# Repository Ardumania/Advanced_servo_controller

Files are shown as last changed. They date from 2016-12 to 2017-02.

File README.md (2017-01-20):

# Advanced_servo_controller
Based on ATtiny85 and PJON bus

In the last years I have worked in several projects related with education and robotics 
and I have found several problems, if you work with only one microcontroller you are very 
limited about the number of servos you can drive, you need a separate controller to 
drive until 32 servos, but it’s still possible. What about sensors? if you are planning 
to build an hexapod and mount two distance sensor for each leg It’s practically impossible.

There are systems for robotics that consist in smart servos connected by a RS-485 bus 
(Dynamixel or Ubtech), but in these systems is not possible to implement sensors on the 
same bus. And other problem is that those systems use a closed protocol and developers 
can’t implement their own sensors or actuators.

For several time I was thinking in an alternative system for implement sensors and actuators 
in a same communication bus and, of course, do it open allowing developers and enthusiast to 
design their own modules and share them. Initially thought in I2C bus be cause is well 
documented and easy to use but need 4 wires and there are no standard cable to use, this 
is an inconvenient.

In May 2015 I was talking in Valencia with my mentor and friend David Cuartielles about 
this project and he made me a suggestion: the PJON bus developed by an italian guy 
(Giovanni Blu), it’s one wire, addressable, fully bi-directional and open. That was 
instant love and this project could start.
PJON project can be found here: https://github.com/gioblu/PJON

The main goal of this project is to build a net of modules that can talk to each others
and with the main controller by only a one wire. Just think about it: one wire for data, 
one wire for GND and another wire for VCC, you can have a net of actuators and sensors 
just connected by standard servo wires… and can be connected up to 256 devices.

The first prototype is a servo module, actually called Advanced Servo Controller, and 
is in a very early state of development but it will work for sure be cause the concept 
is very simple: a small pcb with an ATtiny85 that communicates with a main controller 
(Arduino, of course) via a PJON bus, this ATtiny receives commands and generates the 
servo control signals. Commands can be like AT commands, e.g. “GT1500,2000”, this is 
Go To position 1500 in 2000 milliseconds, position is the servo control signal duty 
cycle in microseconds and final time is the time in which must reach that position 
from its actual position… simple. Each module has a current sensor a can send readings 
to the main controller as responses to a specific requests… and more capabilities can 
be implemented in the module firmware in the future.

In the future can be implemented more types of modules with sensors, e.g. distance sensors, 
which are very interesting in robotics.

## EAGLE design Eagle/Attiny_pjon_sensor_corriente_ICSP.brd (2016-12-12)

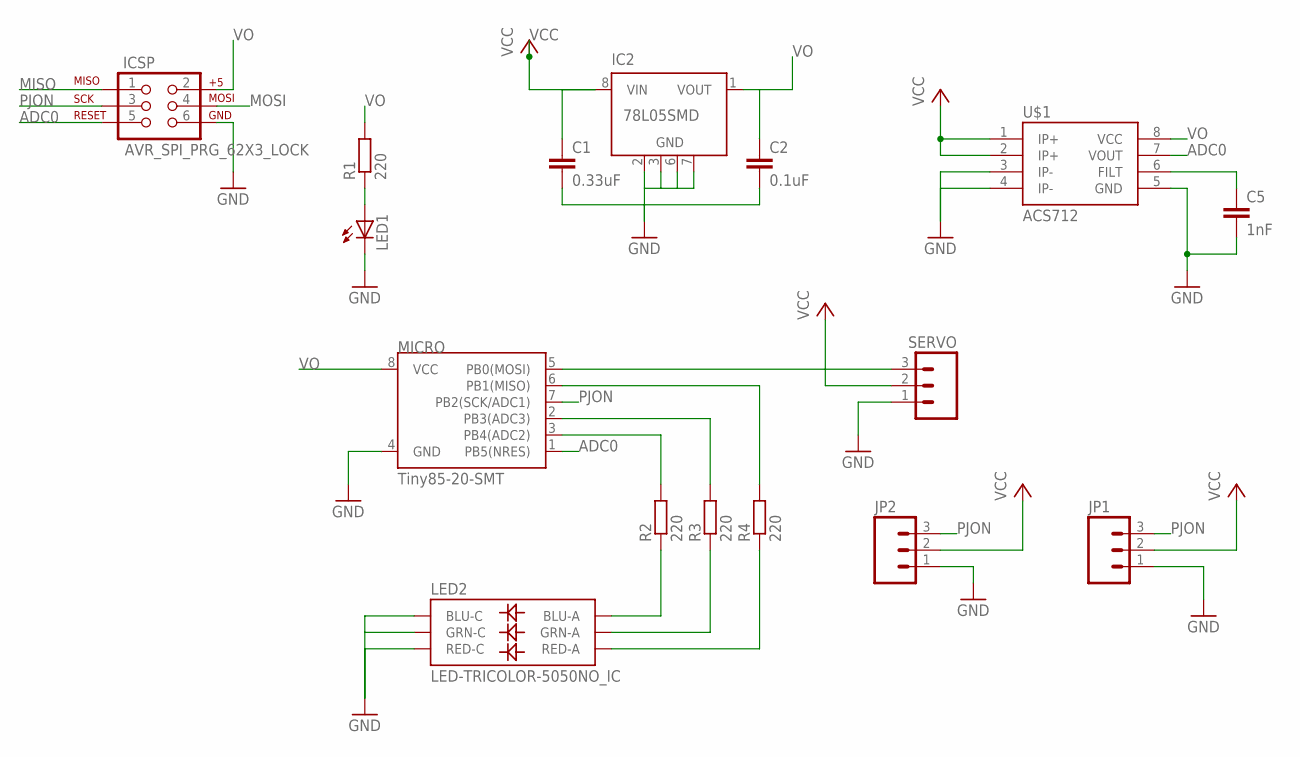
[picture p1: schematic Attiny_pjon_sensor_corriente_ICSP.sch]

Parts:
C1: 0.33uF; C1206
C2: 0.1uF; C1206
C5: 1nF; C1206
IC2: 78L05SMD; SO08
ICSP: AVR_SPI_PRG_62X3_LOCK; 2X3_LOCK
JP1, JP2: M03PTH; 1X03
LED1: LEDSMT1206; 1206
LED2: LED-TRICOLOR-5050NO_IC; LED-TRICOLOR-5050
MICRO: Tiny85-20-SMT; SO08-EIAJ
R1, R2, R3, R4: 220; R1206
SERVO: M03PTH; 1X03
U$1: ACS712; SO08

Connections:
ADC0: ICSP.5, MICRO.1 (PB5(NRES)), U$1.7 (VOUT)
GND: C1.2, C2.2, C5.2, IC2.2 (GND), IC2.3 (GND), IC2.6 (GND), IC2.7 (GND), ICSP.6, JP1.1, JP2.1, LED1.C, LED2.4 (BLU-C), LED2.5 (RED-C), LED2.6 (GRN-C), MICRO.4 (GND), SERVO.1, U$1.3 (IP-), U$1.4 (IP-), U$1.5 (GND)
MISO: ICSP.1, MICRO.6 (PB1(MISO)), R4.2
MOSI: ICSP.4, MICRO.5 (PB0(MOSI)), SERVO.3
unnamed: MICRO.3 (PB4(ADC2)), R2.2
unnamed: C5.1, U$1.6 (FILT)
unnamed: MICRO.2 (PB3(ADC3)), R3.2
unnamed: LED2.3 (BLU-A), R2.1
unnamed: LED2.1 (GRN-A), R3.1
unnamed: LED2.2 (RED-A), R4.1
unnamed: LED1.A, R1.1
PJON: ICSP.3, JP1.3, JP2.3, MICRO.7 (PB2(SCK/ADC1))
VCC: C1.1, IC2.8 (VIN), JP1.2, JP2.2, SERVO.2, U$1.1 (IP+), U$1.2 (IP+)
VO: C2.1, IC2.1 (VOUT), ICSP.2, MICRO.8 (VCC), R1.2, U$1.8 (VCC)

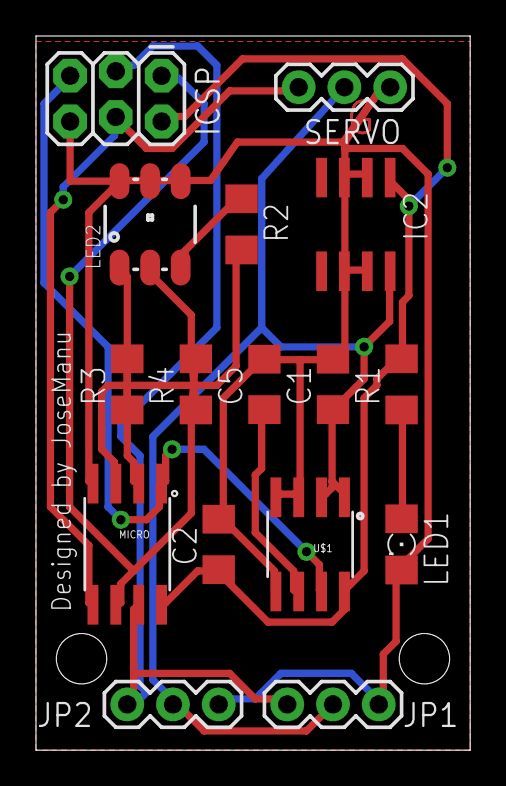
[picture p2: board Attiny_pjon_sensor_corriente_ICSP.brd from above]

Board: 2 copper layers, 24.1 x 39.7 mm, 16 parts (0 on the bottom side), 14 nets.

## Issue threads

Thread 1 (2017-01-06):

External oscillator

gioblu, 2017-01-06:
Ciao, I think could be safer to use an external oscillator to have also large batches of those devices working in the same fashion. Sadly the internal oscillator (or PPL clock) is not so reliable and it can have strong differences  in behaviour, chip to chip. so having some of them not working or operating at a lower performance. Using a 16MHz external oscillator would enable the ATtiny to run SoftwareBitBang at FAST_MODE so at  25157Bd or 3.15kB/s. See https://github.com/gioblu/PJON/wiki/ATtiny-interfacing and https://github.com/gioblu/PJON/issues/25

Ardumania, 2017-01-10:
Hi @gioblu, I am very honored that you follow this project and all your suggestions will be taken into account.
This is the first version of the board and there are many things to change, first of all the RGB LED goes out. Another contributor suggest that will be a great idea to have a temperature sensor on board and I must to put a NTC resistor.
I'm redesigning the board at this moment and it's a good moment for your suggestion, I'm going to put a 16MHz external oscillator.
 I have all the materials for the first version and will mount only 2 or 3 units for test.
Thank you very much.

gioblu, 2017-01-10:
Ciao @Ardumania, I am honored too to see PJON being your choice for this project.
Feel free to contact me for info/support.

gioblu, 2017-01-11:
I forgot to mention, that years ago I worked on a really small Arduino compatible board, based on ATtiny85 (ATtiny85 + 78l05 + 2 caps + LED + resistor) was able to run smoothly cheap servos: https://www.youtube.com/watch?v=PxwNOG1WzhY
In any case, PJON needs the external oscillator, but I think this is an indication that you will be able to achieve your goal, to reduce buzz or jitter:
- Detach servos when not moving
- Power servo not from 5v, but with external power supply 5/6v
- If using common power supply, power servos through a diode, blocking current to flow from the servo to the power supply.

gioblu, 2017-01-11:
@Ardumania, temperature sensor is cool, but would be nice in some cases to have the chance to drive 2 servos, for example where you need to drive 2 wheels precisely (rover robot), so with a single packet it would be possible to start both wheels at a determined speed, at the same time.

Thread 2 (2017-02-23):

Circuit considerations

gioblu, 2017-02-23:
Ciao @Ardumania I have taken a look to the new board schematic you pushed.
I maybe have a wrong feeling but, wouldnt the diode be better positioned before VIN instead of after VOUT? I generally have needed a diode in that configuration to share power supply with a running servo with an arduino. Maybe higher capacitance capacitor on power supply would for sure help to mantain voltage stability.

Ardumania, 2017-02-23:
Ciao @gioblu , I appreciate your suggestions.
With the first circuit version was a problem, when connected the ArduinoISP to program the ATtiny the voltage regulator burned because power of ArduinoISP and voltage regulator output were not compatible. Adding a schottky diode this problem is now solved.
You are right, in this configuration VOUT is 4,5v, the minimum voltage to work, but it works.
My knowledge of electronics are very poor, so I don't know very well what I'm doing, but at this moment woks.
The servo must receive VCC without passing through voltage regulator, i.e. direct power from the battery. I don't understand very well your suggestion about a blocking diode on attiny side but I will search about information about this, as I said I'm a little lost with electronics.
In few days I will start to work with a small servo.
Thank you.

gioblu, 2017-02-23:
@Ardumania  I am sorry for the italianizations hehe :).

I would try to feed the voltage regulator though a diode positioned there to "block" inverse current before the power supply stage, removing the diode you now have on VOUT. And with this you should have shielded your regulator VOUT by strong voltage oscillations due to the servo running. I do think that in this configuration the servo motor voltage drop would affect less the capacitors, so giving you a more stable VOUT. I agree that the servo shouldnt be powered by the voltage regulator, because it has its own.

I have never had a 7805 / 78l05 burning for that reason, are you sure there was some other hidden issue? In general if flashed from another arduino and arduinoISP 78l05 survives and should work fine without any additional hardware in that configuration.

Consider that a lower than 5 volts affects the maximum distance range you can get with PJON communication range to have 5v as a reference to avoid to affect PJON communication range.

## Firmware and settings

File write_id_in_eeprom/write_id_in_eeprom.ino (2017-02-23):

/*
 * EEPROM Write for Advanced Servo Controller
 * by Jose Manuel Escuder
 * ver 0.1 February 23th, 2017
 * License (CC)BY-NC-SA
 * 
 * This firmware must be uploaded to the module using a ArduinoISP
 * or a Arduino UNO as ISP programmer.
 * In the Tools menu select "ATiny25/45/85" as board, then select 
 * "ATtiny85" as processor and at last select "External 16MHz" as clock
 * 
 * To upload this program select "Upload using programmer" in the Program menu.
 * Be sure you have the right programmer selected in the Tools menu.
 * 
 * This program store the number 10 into the EEPROM in 
 * position 0. That number will be the id of this device.
 * If you want to save another id just modify the value in
 * line 28.
 * 
 * Once work is done you can see a blink in the servo pin
 * if connect a LED between it and GND
 */

#include <EEPROM.h>

void setup(){
  
  pinMode(0, OUTPUT);
  // Save number 10 (id) in position 0
  EEPROM.write(0, 10);
}

void loop(){
  // The work is done, now just blink pin 0
  digitalWrite(0, HIGH);
  delay(500/16);
  digitalWrite(0, LOW);
  delay(500/16);

}

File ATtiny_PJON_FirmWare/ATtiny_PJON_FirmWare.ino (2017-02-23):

/*
 * Advanced Servo Controller Firmware
 * by Jose Manuel Escuder
 * ver 0.1 January 20th, 2017
 * License (CC)BY-NC-SA
 * 
 * This firmware must be uploaded to the module using a ArduinoISP
 * or a Arduino UNO as ISP programmer.
 * In the Tools menu select "ATiny25/45/85" as board, then select 
 * "ATtiny85" as processor and at last select "External 16MHz" as clock
 * 
 * To upload this program select "Upload using programmer" in the Program menu.
 * Be sure you have the right programmer selected in the Tools menu.
 * 
PhysicalPin  ATtiny Pin       Function
    1         reset             can't use
    2         digital 3, A3     Xtal
    3         digital 4, A2     Xtal
    5         digital 0 (PWM)   servo signal
    6         digital 1 (PWM)   PJON Bus
    7         digital 2, A1     ADC1
 */

// do a more efficient use of memory changing the defect values by
// these new, the maximum number of packets this module can handle
// is 2 and these packets has a limited length of 5 bytes
#define MAX_PACKETS 2
#define PACKET_MAX_LENGTH 5

#include <PJON.h>

#include <EEPROM.h>

PJON<SoftwareBitBang> bus;

int positionToGo, actualPosition;
int timeToGo;

void setup() {
  // the device id is stored in the EEPROM,
  // in the position 0, going to read it and
  // set it as bus id. If the module is new the 
  // id by default is 10
  int id;
  EEPROM.get(0, id);
  bus.set_id(id);

  // The pin bus is 3
  bus.strategy.set_pin(3);
  // Set what to do when a request is received
  bus.set_receiver(receiver_function);
  // Start communication
  bus.begin();
}

void receiver_function(uint8_t *payload, uint16_t length, const PacketInfo &packet_info) {
  // command GoTo, reach a new position in a determined time
  if(char(payload[0]) == 'G'){ 

    positionToGo = byte(payload[1]);
    positionToGo = positionToGo << 8;
    positionToGo |= byte(payload[2]);
    
    timeToGo = byte(payload[3]);
    timeToGo = timeToGo << 8;
    timeToGo |= byte(payload[4]);
  }

  // command Read, read the ACS712 and send a response to the master
  if(char(payload[0]) == 'R'){
    int lecture = analogRead(A1);
    char content[2] = {lecture >> 8, lecture & 0xFF};
    bus.reply(content, 2);
    bus.update();
  }

  // command NewId, change the module Id 
  if(char(payload[0]) == 'N'){
    int newId = byte(payload[1]);
    EEPROM.put(0, newId);
    bus.set_id(newId); 
  }
}

void loop() {
  bus.receive();

  /*
   * now move the servo... work in progress
   * 
   */
};

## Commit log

2016-12-12 Ver 0001
    Nothing of this works, it's only a prove of concept
    [Attiny_pjon_sensor_corriente_ICSP.brd, Attiny_pjon_sensor_corriente_ICSP.csv, Attiny_pjon_sensor_corriente_ICSP.sch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]
2016-12-15 ver 0002
    [Attiny_pjon_sensor_corriente_ICSP_compra.ods]
2016-12-19 Folder name changed
    [Attiny_pjon_sensor_corriente_ICSP.brd, Attiny_pjon_sensor_corriente_ICSP.csv, Attiny_pjon_sensor_corriente_ICSP.sch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]
2016-12-19 Actualización de README
2017-01-10 Board V0.2
    RGB LED Removed.
    Added external oscillator, temperature sensor and a center hole
    [Attiny_pjon_sensor_corriente_ICSP.csv, Attiny_pjon_sensor_corriente_ICSP_compra.ods, Attiny_pjon_v02.brd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]
2017-02-23 Scheme V02
    Fixed an issue related with voltage regulator, tested in bread board
    [Attiny_pjon_v02.brd, Attiny_pjon_v02.sch]
2017-02-23 Small program to save the id in a device

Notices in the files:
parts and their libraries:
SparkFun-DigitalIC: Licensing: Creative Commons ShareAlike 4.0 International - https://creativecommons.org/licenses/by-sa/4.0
